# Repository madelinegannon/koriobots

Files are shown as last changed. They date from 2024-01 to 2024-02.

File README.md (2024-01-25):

# Koriobots
Koriobots are **cable-driven robots** that can be **dynamically choreographed** to make things float through mid-air. 
The koriobot platform is an open source toolkit aimed at unlocking **more imaginative experiences in robotics**: it is designed so that artists, architects, and designers can bring their creativity to **blend digital experiences with physical spaces**.

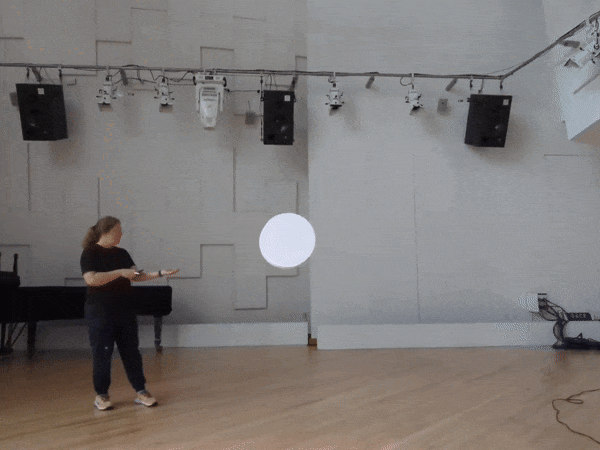
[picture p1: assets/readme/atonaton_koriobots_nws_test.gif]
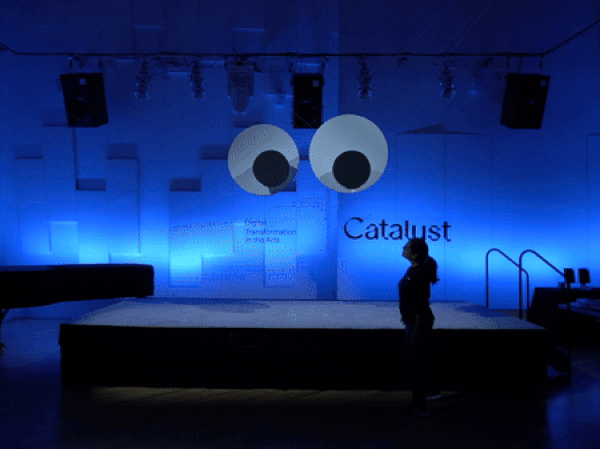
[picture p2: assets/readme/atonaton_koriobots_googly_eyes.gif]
|  |  |
| --- | --- |

## Overview
This reposity contains all the learning materials, fabrication files, BOMs, and software to create your own cable-driven robot systems. 

- See the [software](https://github.com/madelinegannon/koriobots/tree/main/software) directory for the koriobots server, third-party software templates, and example projects.
- See the [hardware](https://github.com/madelinegannon/koriobots/tree/main/hardware) to see the BOM and download 3D printable parts for making your own koriobots.
- See the [tutorials](https://github.com/madelinegannon/koriobots/tree/main/tutorials) directory to learn how to make and use koriobots.

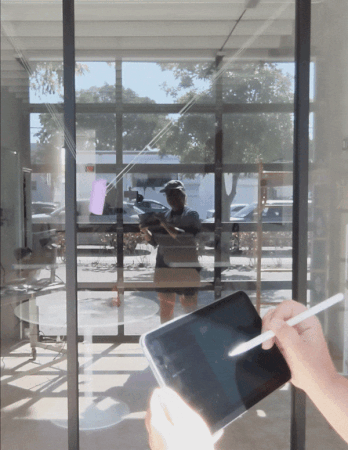
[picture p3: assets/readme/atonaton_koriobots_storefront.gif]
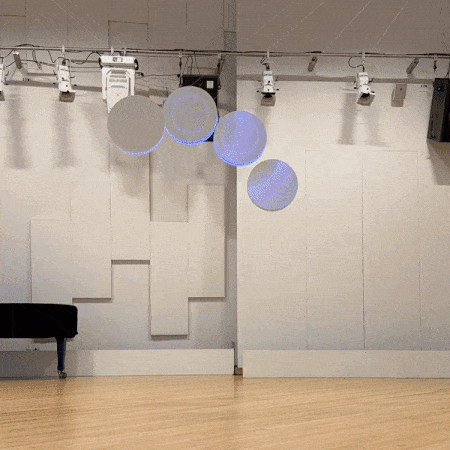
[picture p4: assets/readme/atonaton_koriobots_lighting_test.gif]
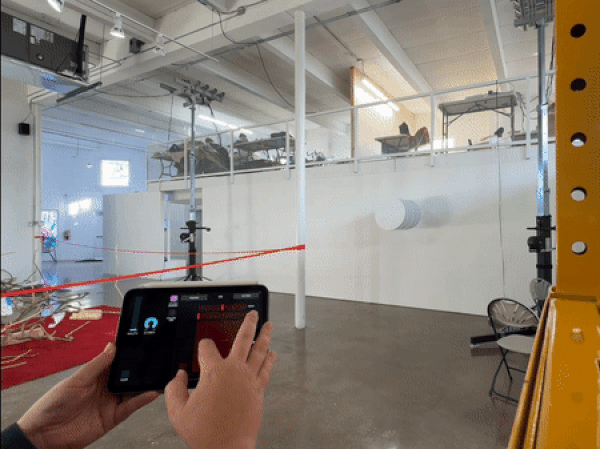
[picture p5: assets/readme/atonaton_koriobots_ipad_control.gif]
|  |  |  |
| --- | --- | --- |

## Motivations
Koriobots is intended as a functional, replicatable, and extensible reference design for professional-grade cable robots. The specified hardware strives to be more reliable _(and expensive)_ than DIY solutions, and more flexible, deployable _(and cheaper)_ than comparable industrial solutions. The control software is developed with interaction and performance at its core: it is extensible to external creative programming environments, and can be configured with automatic startup, homing, and shutdown for standalone art installations.

Cable-driven robots are the secret ingredient for many of the most magical and engaging kinetic installations of the past twenty years. Unfortunately, each artist group has had to build their own cable robots from scratch. By sharing this knowledge, we can spend less 
 time reinventing technical solutions, and more time on creative exploration. 

| _[Otto (2014~)](https://juerglehni.com/works/otto)_ by [Jürg Lehni](https://juerglehni.com/works) | _[Pendulums V (2015)](https://artcom.de/en/?project=pendulum-casa-v)_ by [ART+COM](https://artcom.de/en/department/art-en/) | _[In 20 Steps (2015)](https://studiodrift.com/work/in-20-steps/)_ by [Studio Drift](https://studiodrift.com/works/) | _[Kinds of Life (2019)](https://www.random-international.com/kinds-of-life)_ by [Random International](https://www.random-international.com/work) |
| --- | --- | --- | --- |
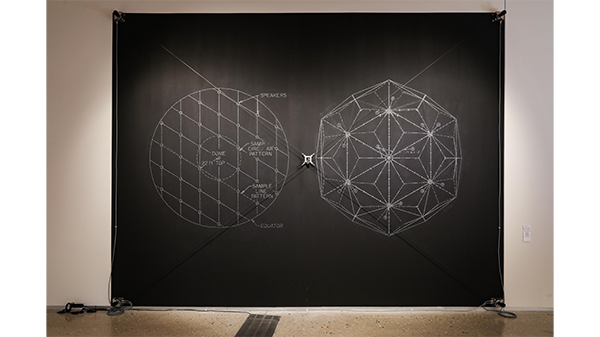
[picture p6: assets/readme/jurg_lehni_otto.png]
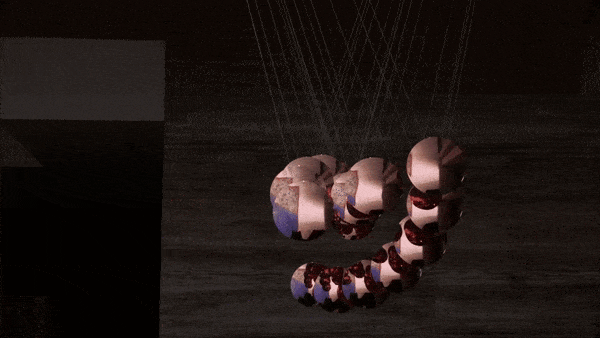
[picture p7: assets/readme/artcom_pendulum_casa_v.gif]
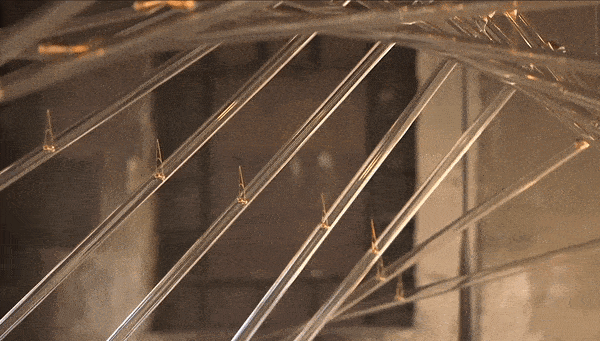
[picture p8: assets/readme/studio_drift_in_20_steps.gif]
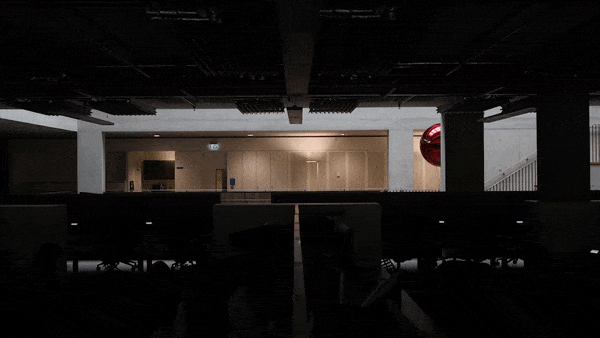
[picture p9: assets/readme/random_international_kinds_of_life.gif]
|  |  |  |  |

Our hope is that this knowledge repository can mitigate many of the technical hurdles of working with cable robots, and help to spark new forms of creative inquiry with this special type of robotic system.

## Contributing
The goal of this open source project is to grow and support many more usecases and audiences for cable-driven robots. We invite any and all contributions that extend the hardware, software, and learning materials for koriobots. Here are a few requests:
- Hardware
  - Additional mechanical design options for the cable drum.
  - Additional mounting options.
  - Additional end-effectors.
  - Alternative sources and specifications for the BOM.
- Software
  - Support for non-Teknic motors.
  - Improved velocity and position controllers.
  - Additional templates for third-party software integrations.
  - Additional examples showcasing different use cases and learning concepts.

## Acknowledgements
Koriobots was made possible through generous support from the [Knight Foundation](https://knightfoundation.org/challenges/knight-new-work/).
Special thanks to the [FIU RDF Lab](https://carta.fiu.edu/roboticslab/), [New World Symphony](https://www.nws.edu/), [Oolite Arts](https://oolitearts.org/), and [Locust Projects](https://www.locustprojects.org/) for housing our experiments throughout the development of this project. 

Koriobots was developed with [openFrameworks](https://openframeworks.cc/), an open source C++ toolkit for creative coding.

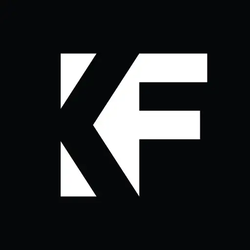
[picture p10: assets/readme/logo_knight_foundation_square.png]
Knight Foundation Logo
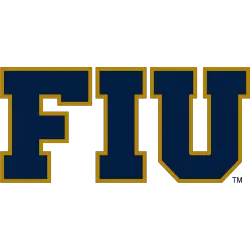
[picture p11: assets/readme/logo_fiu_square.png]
FIU Logo
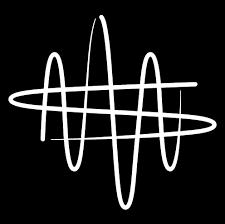
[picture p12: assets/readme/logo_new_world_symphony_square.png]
New World Symphony Logo
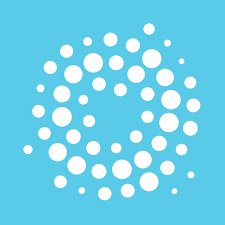
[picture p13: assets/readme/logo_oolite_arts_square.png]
Oolite Arts Logo
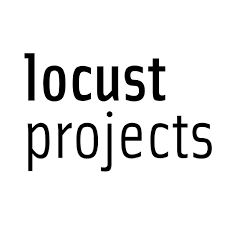
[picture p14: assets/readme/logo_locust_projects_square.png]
Locust Projects Logo
|  |  |  |  |  | 
| --- | --- | --- | --- | --- |

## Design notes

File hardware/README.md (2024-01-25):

# Koriobots Hardware

## Overview
The hardware of a Koriobots system is made up of the following components:

- Grooved Cable Drum
- Motor Controller
- Cable & Pulley
- Mounting Components
- End-Effector

Assemble the parts and prints following the [Assembly Tutorial](https://github.com/madelinegannon/koriobots/tree/main/hardware).

### Grooved Cable Drum
Each Koriobot uses a [grooved cable drum](https://wirerope.net/azwr/drums/#:~:text=%EF%80%82-,Drums%20%E2%80%93%20Grooved,-Drums%20are%20the) to reliably wind and unwind their cable. This cable-drum design was developed with mechanical simplicity and ease of production in mind. It features a [ClearPath-SC](https://www.teknic.com/files/downloads/Clearpath-SC%20User%20Manual.pdf) all-in-one servo motor system with full software control, a 3D printed grooved cable drum designed for 0.33mm diameter cable, and a shaft, couplings, standoffs and 3D printed mounts to connect everything together.

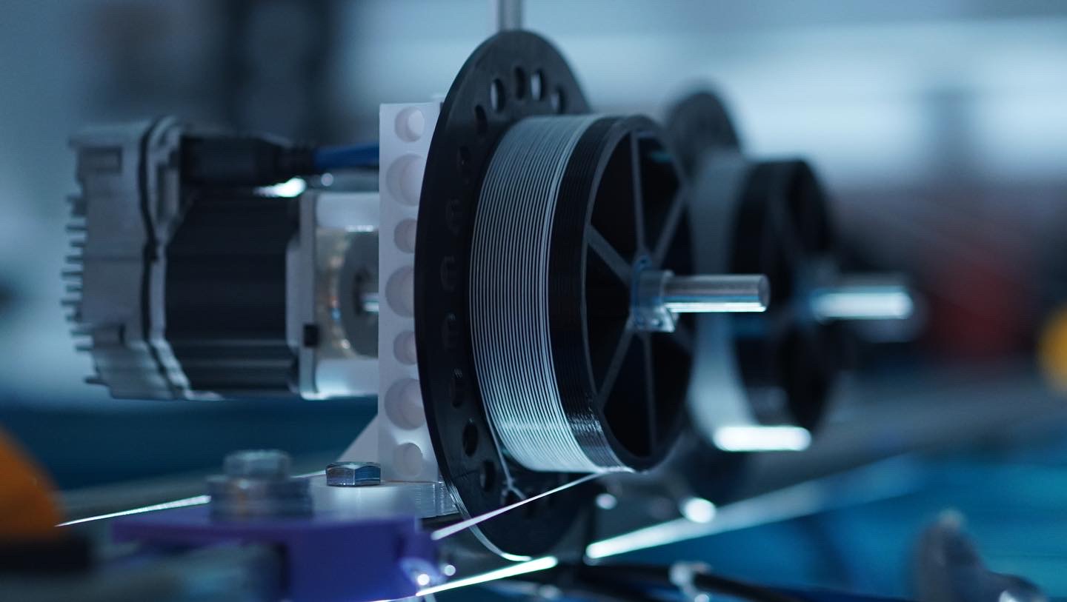
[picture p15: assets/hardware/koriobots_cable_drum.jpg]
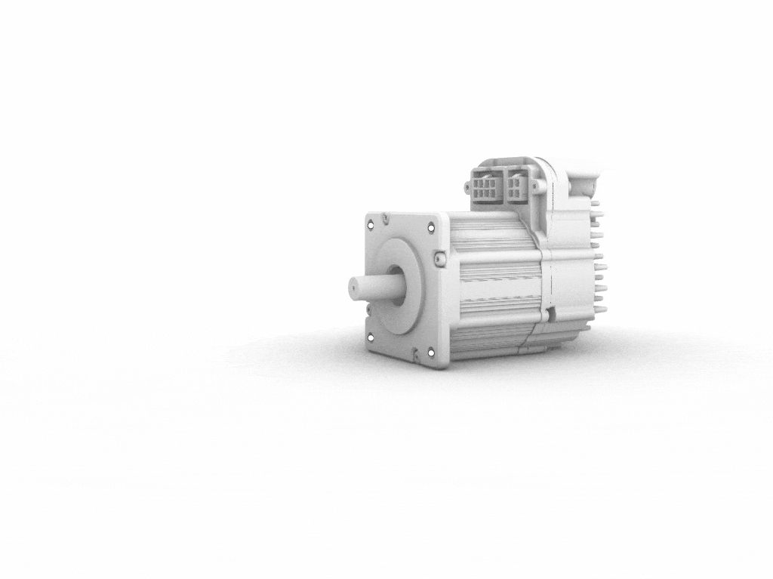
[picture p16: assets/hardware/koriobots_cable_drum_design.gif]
|  |  |
| --- | --- |

The provided 3D printed grooved cable drum holds over 6 meters (20 feet) of cable. You can modify the design of the drum to hold more or less cable based on your needs. 

### Motor Controller
Koriobots use the boards, cables, and power supplies specified by Teknic for their [ClearPath-SC](https://teknic.com/products/clearpath-brushless-dc-servo-motors/clearpath-sc/scsk-models/) motors. See the [BOM](https://github.com/madelinegannon/koriobots/tree/main/hardware/BOM.md) and Teknic's [ordering guide](https://teknic.com/clearpath-accessories-guide/accessories-guide-sc-dc/#overview) for complete list of required parts.

> The [`Manual_12oz_800_L.mtr`](https://github.com/madelinegannon/koriobots/blob/main/hardware/Manual_12oz_800_L.mtr) configuration file is here only as a reference. You should calibrate each of your motors based on your specific build, following Teknic's [instructions](https://www.teknic.com/files/downloads/Clearpath-SC%20User%20Manual.pdf) (page 52).

| [Communication Hub](https://teknic.com/SC4-HUB/) | [Power Hub](https://teknic.com/POWER4-HUB/) | [Motor Power Supply]() | [Logic Power Supply]() |
| --- | --- | --- | --- |
|  |  |  |  |
| Provides network connection for up to four ClearPath-SC motors. | Distributes DC bus power to up to four ClearPath motors. | Low Voltage (75 VDC) power supply for motor drive bus power. | General purpose logic power supply. |

### Cable & Pulley
Koriobots precisely position their end-effector by synchronously winding and un-winding their cables. We recommend using braided fishing line for light-weight applications. We have found that it is stiffer and stronger than conventional monofilament, and more available and pliable than thin-diameter wire cable. We have tested with [Sufix Advanced Superline 832 Braid 80lb](https://www.rapala.com/us_en/832-advanced-superline?childSku=us-660-080GH).

We integrate a small pulley for more precise positioning and routing of the cable. We've found it also helps prevent the cable drum from unspooling should the line lose tension. 
> Position the pulley at least 450mm (~18") from the cable drum for optimium spooling and unspooling.

### Mounting Components
We provide 3D printed files for mounting Koriobots to 3/8"-16 and M8 compatible fixtures, such as Unistrut, 45mm t-slot aluminum, and standard grip gear (like truss clamps).

|  |  |  |
| --- | --- | --- |

### End-Effectors
The end-effector is the thing that the koriobots are moving. You design this component based on your use case. Here are a few things to consider with your design:
- The Koriobots should connect at the Center of Mass of your end-effector.
- The end-effector will move more fluidly if its weight is symmetrically and bilaterally balanced.
- The end-effector should be heavy enough to keep the cable in tension throughout operation.
- The end-effector should not exceed the following recommend payloads that we have tested with this hardware design.

Maximum recommended payloads per configuration:
- 1D: 340g (0.75lb)
- 2D: 680g (1.50lb)
> _Note:_ The motors will overheat and shut off if overloaded, which will result in your payload falling.

[Plumb bobs](https://en.wikipedia.org/wiki/Plumb_bob) are a great default end-effector to start: they can be purchased in a number of weights and are symmetrical.

## Getting Started

1. Reference the [BOM](https://github.com/madelinegannon/koriobots/tree/main/hardware/BOM.md) to order the required parts.
2. Print the 3D models in the [`/cad_files`](https://github.com/madelinegannon/koriobots/tree/main/hardware/cad_files) folder.
3. Assemble the parts and prints following the [Assembly Tutorial]().

## Contributing
This design optimizes for mechanical simplicity, not efficiency. We welcome additional designs that maximize the torque, velocity, and mechanical efficiency of the cable drum design.

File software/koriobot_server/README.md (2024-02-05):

# Koriobot Server

The koriobot server is a software backend for controlling and coordinating teams of koriobots. You can run the server and communicate over OSC from many third-party applications, like Blender, TouchDesigner, Rhino/Grasshopper, and Unity. 

This README contains information about how to [Setup](https://github.com/madelinegannon/koriobots/tree/main/software/koriobot_server#setup) the sever, how to [Configure](https://github.com/madelinegannon/koriobots/tree/main/software/koriobot_server#configure) your koriobots through `configuration.xml` file, and how to send and receive data using the OSC-based [Sever API](https://github.com/madelinegannon/koriobots/tree/main/software/koriobot_server#server-api).

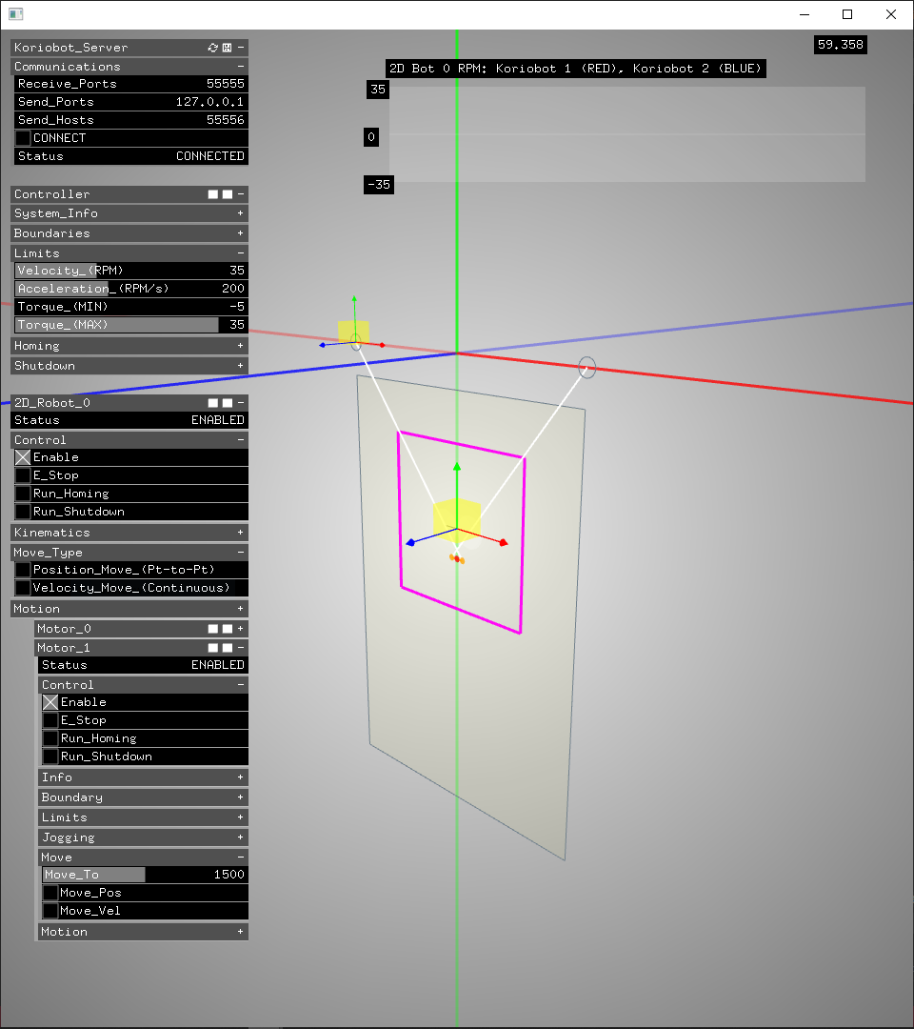
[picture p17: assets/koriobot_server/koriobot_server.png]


### Limitations
The koriobot server is only compatible with Windows 10/11. 

Tested On:
- Windows 10/11
- openFrameworks v0.11.2
- ClearView v1.7.15
- Visual Studio 2022

## Setup
There are two ways to get started using the Koriobot Server: download and install a standalone installer (quickest), or build the project from source code (most customizable).

### Installer

1. Download and install the Teknic ClearView SDK ([.zip file](https://teknic.com/files/downloads/ClearView_Install.zip)).
> _Note:_ If you  want to run ClearPath-SC motors without installing ClearView, just install the Clearpath Port Driver ([.zip file](https://teknic.com/files/downloads/ClearPath%20Port%20Driver%20Install.exe)).
2. Download and install the installer:  `koriobots_server_installer.exe` ([.exe file](https://github.com/madelinegannon/koriobots/blob/main/software/koriobot_server/koriobot_server_installer.exe)).
> _Note:_ If the software doesn't run, you may need to manually download and install the latest Microsoft Visual C++ Redistributable ([vc_redist.x64.exe file](https://aka.ms/vs/17/release/vc_redist.x64.exe)). More info from Microsoft [here](https://learn.microsoft.com/en-US/cpp/windows/latest-supported-vc-redist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).

### Build from Source

The koriobot server is built with [openFrameworks](https://openframeworks.cc/) — an open source C++ toolkit for creative coding — and the Teknic's ClearView SDK for controlling ClearPath-SC Series motors.

1. Download and install the Teknic ClearView SDK ([.zip file](https://teknic.com/files/downloads/ClearView_Install.zip))
2. Download and install [Microsoft Visual Studio 2022](https://visualstudio.microsoft.com/vs/community/)
     - Choose the Desktop Development with C/C++ workload
3. Download and install [openFrameworks v0.11.2](https://github.com/openframeworks/openFrameworks/releases/tag/0.11.2)
4. Install additional third-party addons: [ofxGizmo](https://github.com/NickHardeman/ofxGizmo)
5. Move the folder `/koriobot_server` into your `openFrameworks/apps/myApps` folder and build with the openFrameworks projectGenerator.
6. Build and Run the project in _Release x64_ mode in the IDE.

### Troubleshooting
- [How to install openFrameworks](https://openframeworks.cc/setup/vs/)
- [How to install an openFrameworks addon](https://openframeworks.cc/learning/01_basics/how_to_add_addon_to_project/)
- [How to use the openFrameworks projectGenerator](https://youtu.be/4k2ZcvC0YEA?si=gY0Y-3vlnC-ouL6y&t=252)

#### Teknic ClearPath Motors

- Teknic Downloads Website: https://teknic.com/downloads/
- Direct Download Teknic ClearView SDK [.zip file](https://teknic.com/files/downloads/ClearView_Install.zip)
- Examples are installed here: `C:\Program Files (x86)\Teknic\ClearView\sdk\examples`
- Source code & libraries are installed here: `C:\Program Files (x86)\Teknic\ClearView\sdk\sFoundation Source\sFoundation`

# Configuration File

Configure global settings for the koriobot system using an XML-based configuration file. These parameters are loaded everytime you run server.

- If you used the `Koriobot Server Installer`, your configuration file is located here: `C:\Program Files (x86)\ATONATON\Koriobot Server\data\configuration.xml`.
- If you built the project from source code, your configuration file is located here: `OF_PATH\apps\myApps\koriobot_server\bin\data\configuration.xml`.

The following code block documents what each configuration setting does:

```xml
<config>
    <!--1=1D, 2=2D, 3=3D-->
    <config_type>2</config_type>
    <!--Total number of koriobots-->
    <num_bots>2</num_bots>
    <!--OSC settings to send/receive messages-->
    <osc>
        <receive>
            <port>55555</port>
        </receive>
        <send>
            <host>127.0.0.1</host>
            <port>55556</port>
        </send>
    </osc>
    <!--System origin (in world coordinates)-->
    <origin>
        <X>-875.000000000</X>
        <Y>0.000000000</Y>
        <Z>0.000000000</Z>
        <QX>0.000000000</QX>
        <QY>0.000000000</QY>
        <QZ>0.000000000</QZ>
        <QW>1.000000000</QW>
    </origin>
    <!--Base reference position of each koriobot (in local coordinates)-->
    <bases>
        <pos>
            <X>0</X>
            <Y>0</Y>
            <Z>0</Z>
        </pos>
        <pos>
            <X>1750</X>
            <Y>0</Y>
            <Z>0</Z>
        </pos>
    </bases>
    <!--Motor Indices for 2D Configurations-->
    <motor_pairs>
        <pair>
            <A>0</A>
            <B>1</B>
        </pair>
    </motor_pairs>
    <!--Cable Drum Configuration-->
    <cable_drum>
        <!--1=LEFT-HANDED, 2=RIGHT-HANDED-->
        <direction>1</direction>
        <diameter_drum>99.000000000</diameter_drum>
        <diameter_cable>0.304800000</diameter_cable>
        <length>30</length>
        <turns>40</turns>
    </cable_drum>
    <!--End Effector Configuration-->
    <ee>
        <!--Offset from center of end-effector (in local coordinates)-->
        <offset>
            <X>100</X>
            <Y>0</Y>
            <Z>0</Z>
        </offset>
    </ee>
    <shutdown>
        <!--Position beyond bounds to lower koriobots before shutdown (in local coordinates)-->
        <pos>
            <X>0</X>
            <Y>3000</Y>
            <Z>0</Z>
        </pos>
    </shutdown>
    <!--Centroid, width, height of rectangular motion boundary (in World Coordinates)-->
    <bounds>
        <motion>
            <X>0</X>
            <Y>-1500.000000000</Y>
            <W>1750.0</W>
            <H>2600.0</H>
        </motion>
        <safety>
            <X>0</X>
            <Y>-1000.0</Y>
            <W>1000.0</W>
            <H>1000.0</H>
        </safety>
    </bounds>
    <!--Force Limits-->
    <limits>
        <velocity>35.0</velocity>
        <acceleration>200.0</acceleration>
        <torque>
            <MIN>-5</MIN>
            <MAX>35</MAX>
        </torque>
    </limits>
</config>
```

# Server API

| Message Address | Arg Format | Description |
| --- | --- | --- |
| /stop | —— | Trigger soft stop all koriobots |
| /move_vel | bool | Toggle velocity move on/off for all koriobots |
| /reset | —— | Trigger reset to the center of the safety bounds |
| /norm | int, float, float | Index and normalized {x,y} target coordinate. _Note: use index=-1 to move all koriobots to the normalized target._ |
| /limits/velocity | float | Sets the velocity limit for all koriobots |
| /limit/acceleration | float | Sets the acceleration limit for all koriobots |
| /bounds/pos | float, float | Sets normalized {x,y} position of the safety boundary |
| /bounds/width | float | Sets normalized width of the safety boundary |
| /bounds/height | float | Sets normalized height of the safety boundary |

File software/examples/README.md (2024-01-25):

# Examples
This folder has several useful starter projects in various programming environments. 
- Start the `Koriobot Server` before running these examples.
- See the descriptions below for usage details. 

## Processing
### koriobots_example_mouse2D.pde
Shows how to use your mouse to move the koriobots.
- Hover over the magenta rectangle to move the koriobot target.
- Press and drag the mouse to enable moving.
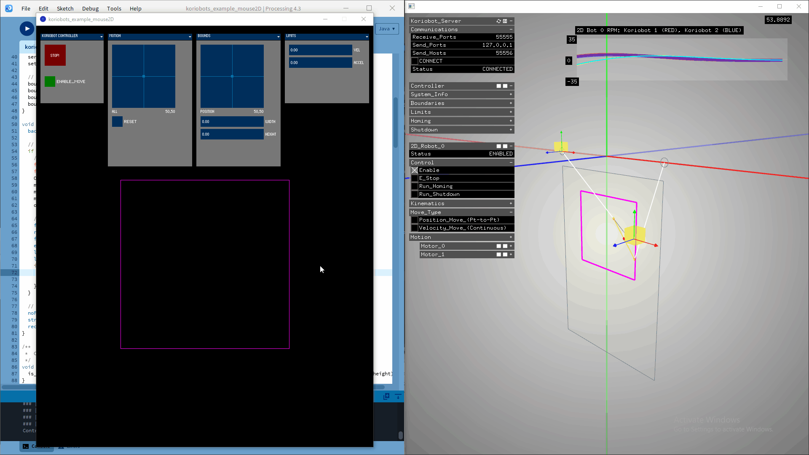
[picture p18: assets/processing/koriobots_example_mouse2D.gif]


### koriobots_example_physics2D.pde
Shows how to use physics simulation to move the koriobots.
- Install the [Box2D-for-Processing](https://github.com/shiffman/Box2D-for-Processing/tree/master/Box2D-for-Processing/dist) library.
- Press and drag the mouse to throw the box around.
- Toggle the `Enable Move` button to enable moving.
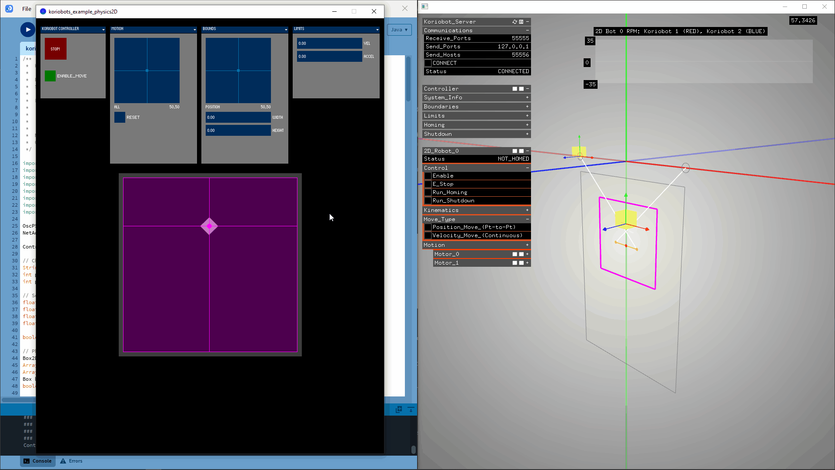
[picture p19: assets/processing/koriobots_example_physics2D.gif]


## Grasshopper
#### koriobots_example_follow_path.gh
Shows how to move the koriobots to follow a path. Useful for pick-and-place operations
- Open _koriobots_example_follow_path.3dm_, start Grasshopper, then open _koriobots_example_follow_path.gh_ inside Grasshopper.
- Update the `Evaulate Curve` slider to move the koriobot target.
- Toggle the `\move_vel` button `ON` to enable moving.
  
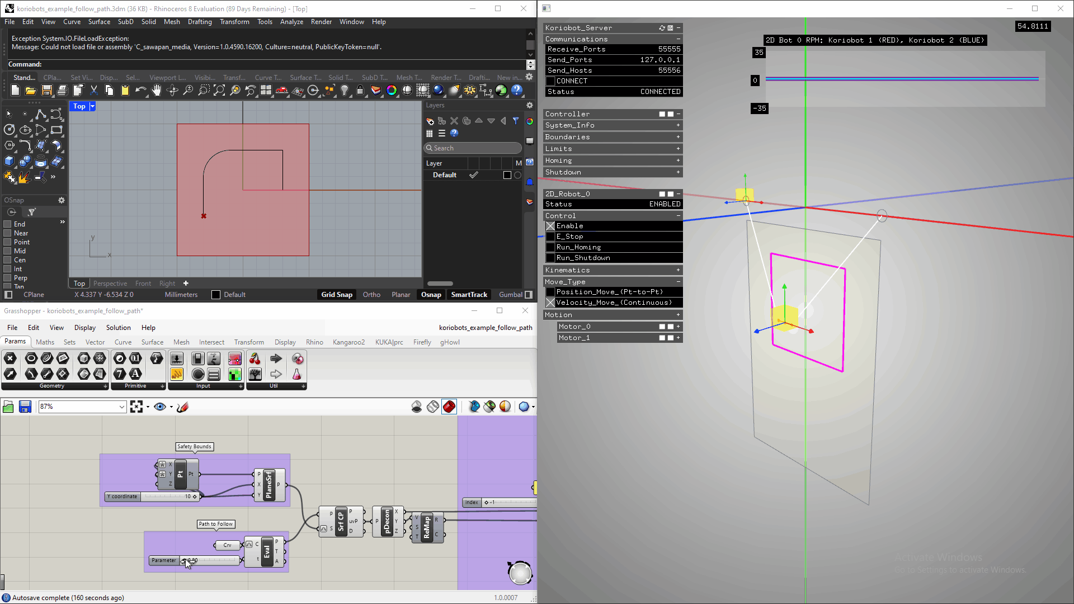
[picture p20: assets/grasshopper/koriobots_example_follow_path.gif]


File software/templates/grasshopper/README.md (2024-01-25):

# Grasshopper Template

[Grasshopper](https://www.rhino3d.com/#:~:text=Kay%2C%20Kiteboard%20Shaper-,Grasshopper,-Grasshopper%20is%20a) is a visual programming environment inside of the popular CAD software, [Rhinoceros 3D](https://www.rhino3d.com/). 

We can use Grasshopper and the [python-osc](https://pypi.org/project/python-osc/) python library to talk to the Koriobot Sever:

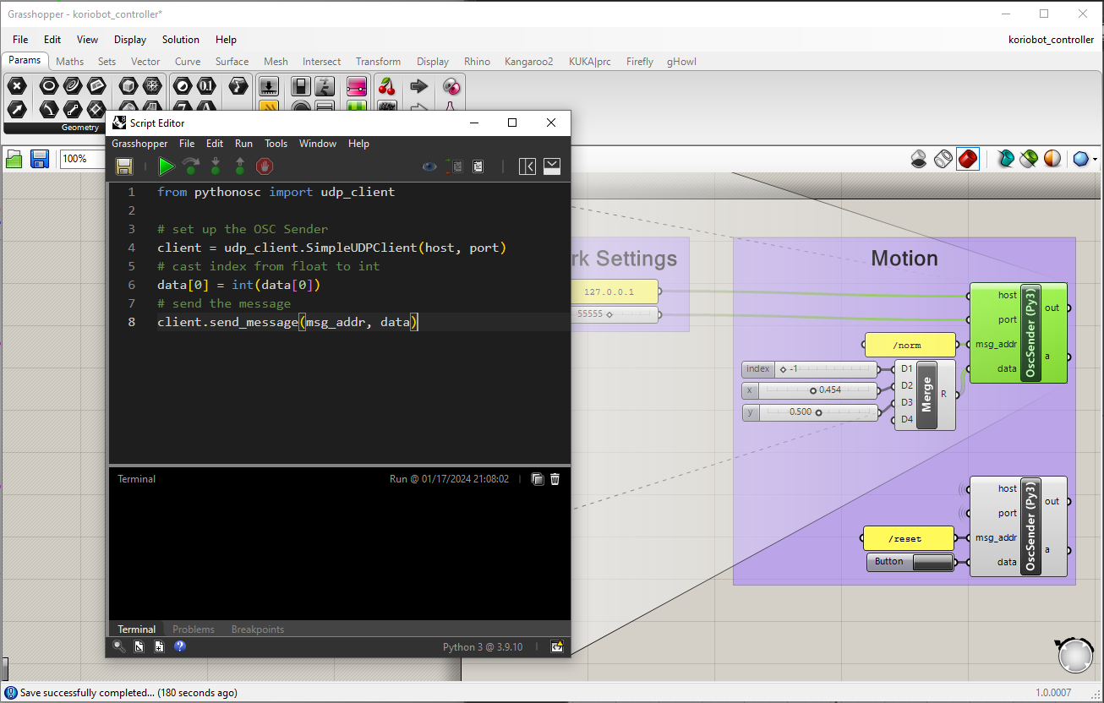
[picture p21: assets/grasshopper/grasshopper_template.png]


## Setup

1. Download and install Rhino 8
> There's a free 90 day trial.
2. Open Grasshopper and add a Python 3 Script to the canvas. 
3. Double Click to open the Python Script Editor.
4. Run the following script to locate where Rhino's contained version of python is stored on your computer:

```
import sys
println(sys.path)
```
> The path should be something like `~\.rhinocode\py39-rh8\`

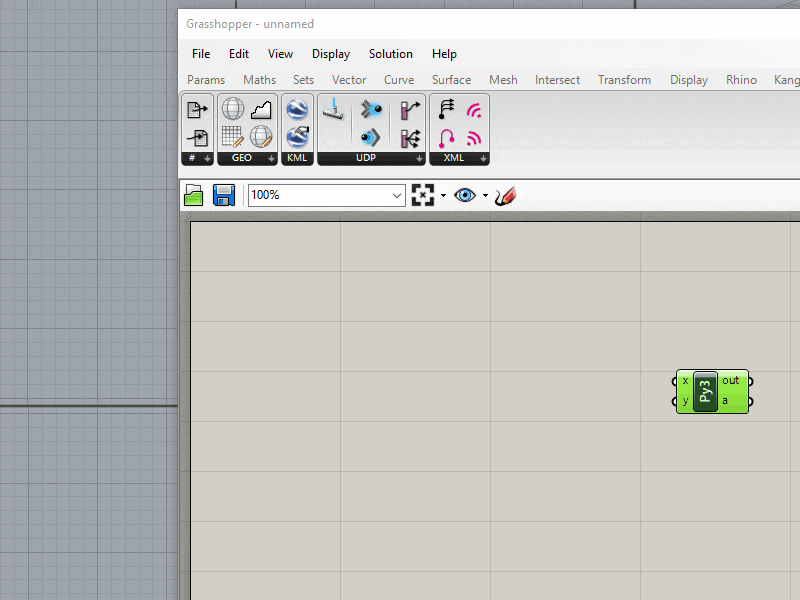
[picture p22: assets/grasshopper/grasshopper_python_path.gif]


5. The `~\.rhinocode\py39-rh8\lib` folder is where we need to add external python libraries for Rhino.
6. Install `python-osc` via pip. Open a terminal, and run the command:

```shell
cd ~\.rhinocode\py39-rh8
pip install --target=.\lib python-osc
```
> You will be prompted to install `pip` if you haven't yet.

### Optional Step:
<details>
<summary>How to manually copy/paste system-wide python library into Rhino's version of python:</summary>
<br>
If the local <b>pip install</b> doesn't work, you can install the library system-wide and copy/paste into Rhino's internal version of python.
<brGo to where `python-osc` was installed, copy the folder, and paste it back into Rhino's internal python library folder.
<br><br> The system-wide library path should be something like <i>~\AppData\Local\Programs\Python\Python310\Lib\site-packages</i>
<br><br>
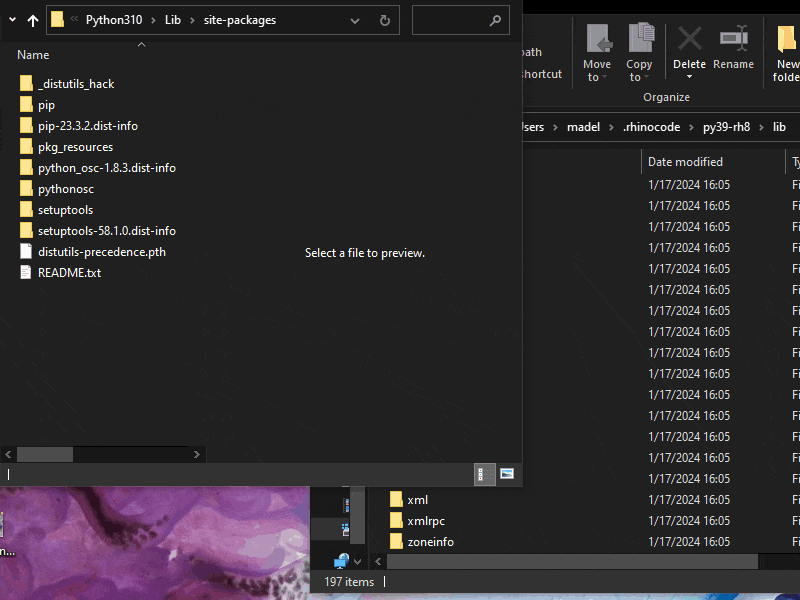
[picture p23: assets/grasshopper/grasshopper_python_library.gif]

</details>

7. Restart Rhino, load Grasshopper, and open `koriobot_controller.gh`. Interact with the sliders or buttons to send a value to the Koriobot Server.

## Notes

- Tested on Windows 10/11, Rhino 8, python 3.9, and python-osc 1.8.3

## Code Reference
These python snippets are the code running inside each of the grasshopper template's _OscSender_ nodes.

```python
# Controls: /stop and /move_vel code
from pythonosc import udp_client

# set up the OSC Sender
client = udp_client.SimpleUDPClient(host, port) 
# send the message       
client.send_message(msg_addr, data)
```

```python
# Motion: /norm code
from pythonosc import udp_client

# set up the OSC Sender
client = udp_client.SimpleUDPClient(host, port)
# cast index from float to int
data[0] = int(data[0])   
# send the message       
client.send_message(msg_addr, data)
```

```python
# Motion: /reset code
from pythonosc import udp_client

# set up the OSC Sender
client = udp_client.SimpleUDPClient(host, port)
# cast index from float to int
data[0] = int(data[0])   
# send the message       
client.send_message(msg_addr, data)
```

```python
# Bounds: /bounds code
from pythonosc import udp_client

# set up the OSC Sender
client = udp_client.SimpleUDPClient(host, port)
 
# send the message
addr = msg_addr + "/pos"  
val = [data[0], data[1]]
client.send_message(addr, val)

addr = msg_addr + "/width"  
val = data[2]
client.send_message(addr, val)

addr = msg_addr + "/height"  
val = data[3]
client.send_message(addr, val)
```

```python
# Motion: /limits code
from pythonosc import udp_client

# set up the OSC Sender
client = udp_client.SimpleUDPClient(host, port)
 
# send the message
addr = msg_addr + "/velocity"  
val = data[0]
client.send_message(addr, val)

addr = msg_addr + "/acceleration"  
val = data[1]
client.send_message(addr, val)
```

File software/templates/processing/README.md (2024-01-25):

# Processing Template

[Processing](https://processing.org/) is a creative coding platform for sketching with code. 

We can use Processing and the third-party library [oscP5](https://sojamo.de/libraries/oscP5/) to talk to the Koriobot Sever:

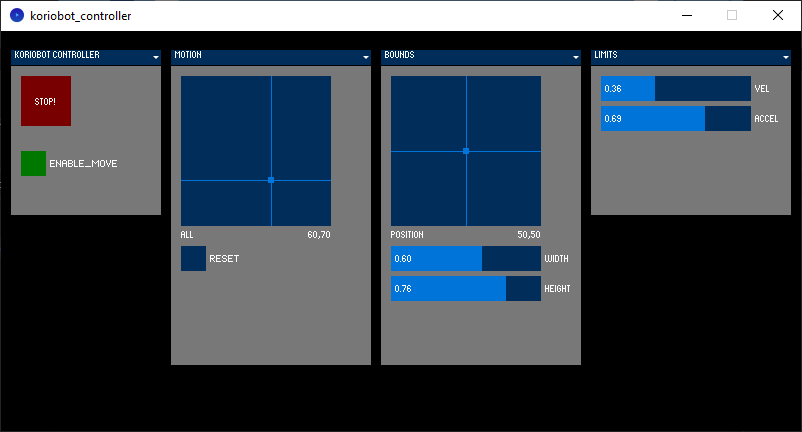
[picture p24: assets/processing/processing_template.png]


## Setup

1. Download and install [Processing](https://processing.org/download).
2. Download and install [oscP5](https://sojamo.de/libraries/oscP5/) following these [instructions](https://sojamo.de/libraries/oscP5/#installation).
3. Copy `koriobot_controller.pde` into your Processing Sketchbook.
4. Configure your network settings:



6. Press play and run.

## Notes

- Tested on Processing 4.3, oscP5 0.9.8, and controlP5 2.2.5

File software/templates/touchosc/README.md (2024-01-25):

# TouchOSC Template

[TouchOSC](https://hexler.net/touchosc) is an easy-to-use interface builder that can send and receive [OSC](https://ccrma.stanford.edu/groups/osc/index.html) messages from multiple sources. It's the quickest way to build your own interactive touch interface on your desktop, phone, or tablet — _plus_ it's supported on nearly every operating system: Windows / macOS / Linux / iOS / Android / RasPi.

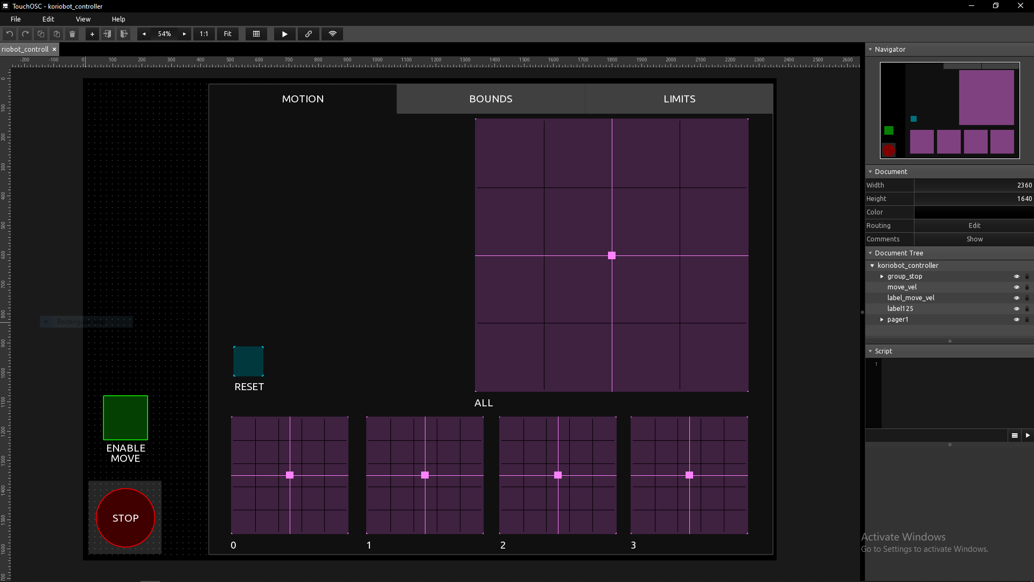
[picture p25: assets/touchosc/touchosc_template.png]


We can use TouchOSC to talk to the Koriobot Sever:



## Setup

1. Download TouchOSC for your platform [here](https://hexler.net/touchosc#get).
> The desktop version is free.
2. Open TouchOSC and configure your network settings.

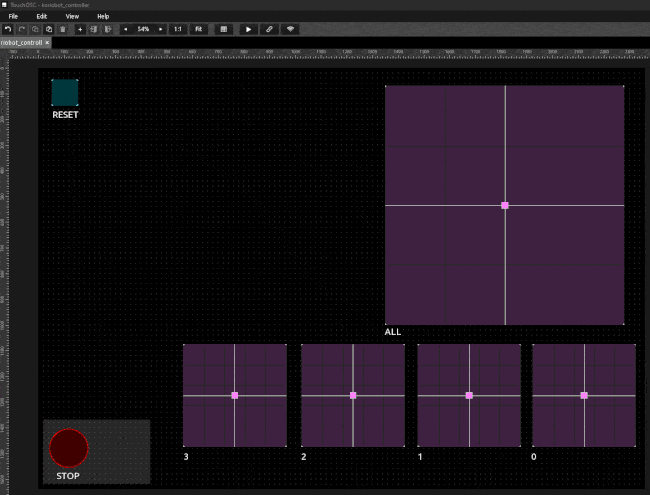
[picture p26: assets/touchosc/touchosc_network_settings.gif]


3. Open a template file in TouchOSC and press the play button to start running the file.
4. Press the dot in the upper right corner to close the file.

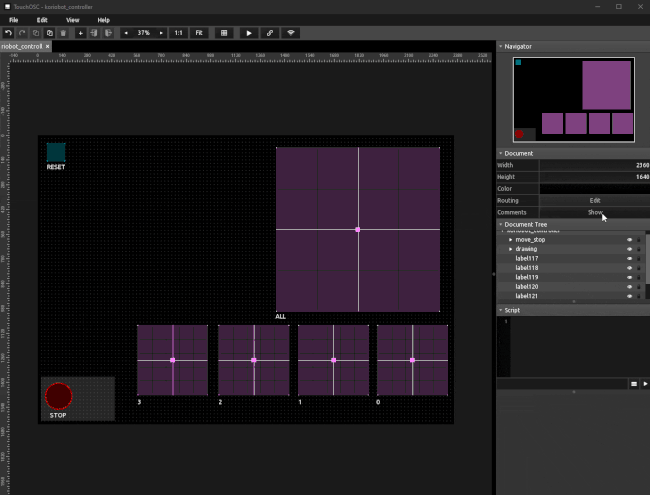
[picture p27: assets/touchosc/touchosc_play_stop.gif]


## Notes

- Tested on TouchOSC 1.2.7.190

## Troubleshooting

- [TouchOSC User Manual](https://hexler.net/touchosc/manual/introduction)

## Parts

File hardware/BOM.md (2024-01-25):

# Bill of Materials

The following table lists the parts and costs for building your own koriobot system. Prices are based in USD for purchases made in 2023. 
One motor is specified in the BOM, however the total cost is not a per-motor cost: there are several items that can be used for multiple koriobots.

We recommend following Teknic's [ordering guide](https://teknic.com/clearpath-accessories-guide/accessories-guide-sc-dc/#overview) to determine the final number of motors, boards, cables, and power supplies needed for your specific system.

🔗 See the google sheet of the following table [here](https://docs.google.com/spreadsheets/d/1K7qIrnV9r5dMJWnOKxVrk1uVV2S3eMcffBsYf00h5N8/edit?usp=sharing).

| Part Name | Sub-Assembly | Part Number | Supplier | Reference | Quantity | Unit Price | Cost | Notes |
| --- | --- | --- | --- | --- | --- | --- | --- | --- |
| ClearPath Integrated Servo Motor | Cable Drum | CPM-SCSK-2310S-RLNA | [Teknic](https://teknic.com/) | [https://teknic.com/model-info/CPM-SCSK-2310S-RLNA](https://teknic.com/model-info/CPM-SCSK-2310S-RLNA) | 1 | $333.00 | $333.00 | Purchase 1 for every ClearPath Motor. |
| Controller Cable, 10 ft | Cable Drum | CPM-CABLE-CTRL-MU120 | [Teknic](https://teknic.com/) | [https://teknic.com/CPM-CABLE-CTRL-MU120/](https://teknic.com/CPM-CABLE-CTRL-MU120/) | 1 | $23.00 | $23.00  | Purchase 1 for every ClearPath Motor. |
| DC Power Cable, IPC (or hub) to ClearPath, 10 ft | Cable Drum | CPM-CABLE-PWR-MS120 | [Teknic](https://teknic.com/) | [https://teknic.com/CPM-CABLE-PWR-MS120/](https://teknic.com/CPM-CABLE-PWR-MS120/) | 1 | $19.00 | $19.00  | Purchase 1 for every ClearPath Motor. |
| 350/500 Watt DC Power Supply | Motor Controller | IPC-5 | [Teknic](https://teknic.com/) | [https://teknic.com/IPC-5](https://teknic.com/IPC-5) | 1 | $248.00 | $248.00 | Purchase 1 for every 8 ClearPath Motors. |
| AC Power Cable for IPC-3 and IPC-5 | Motor Controller | IPC35-CABLE110 | [Teknic](https://teknic.com/) | [https://teknic.com/IPC35-CABLE110/](https://teknic.com/IPC35-CABLE110/) | 1 | $14.00 | $14.00  | |
| Communication Hub for ClearPath-SC Series | Motor Controller | SC4-HUB | [Teknic](https://teknic.com/) | [https://teknic.com/SC4-HUB](https://teknic.com/SC4-HUB) | 1 | $49.00 | $49.00  | Purchase 1 for every 4 ClearPath Motors. |
| 24 VDC Power Supply | Motor Controller | PWR-IO-24VDC | [Teknic](https://teknic.com/) | [https://teknic.com/PWR-IO-24VDC/](https://teknic.com/PWR-IO-24VDC/) | 1 | $39.00 | $39.00  | |
| 24 Volt Power, 2-Pin Molex Cable | Motor Controller | CPM-CABLE-M2P2P-120 | [Teknic](https://teknic.com/) | [https://teknic.com/CPM-CABLE-M2P2P-120/](https://teknic.com/CPM-CABLE-M2P2P-120/) | 2 | $13.00 | $26.00  | |
| DC Power Distribution Hub | Motor Controller | POWER4-HUB | [Teknic](https://teknic.com/) | [https://teknic.com/POWER4-HUB/](https://teknic.com/POWER4-HUB/) | 1 | $49.00 | $49.00  | Purchase 1 for every 4 ClearPath Motors. |
| DC Power Cable, IPC to POWER4-HUB, 6 ft | Motor Controller | PC-SBR-72 | [Teknic](https://teknic.com/) | [https://teknic.com/PC-SBR-72/](https://teknic.com/PC-SBR-72/) | 1 | $18.00 | $18.00  | |
| 3408 Series V-Groove Pulley - 2 Pack | Cable Pulley | 3408-0001-0001 | [ServoCity](https://www.servocity.com/) | [https://www.servocity.com/3408-series-v-groove-pulley-2-pack/](https://www.servocity.com/3408-series-v-groove-pulley-2-pack/) | 1 | $7.50 | $7.50 | |
| 0.375" to 0.375" Clamping Shaft Coupler | Cable Drum | 625064 | [ServoCity](https://www.servocity.com/) | [https://www.servocity.com/0-375-to-0-375-clamping-shaft-coupler-1/](https://www.servocity.com/0-375-to-0-375-clamping-shaft-coupler-1/) | 2 | $5.00 | $10.00  | |
| 0.375" (3/8") x 4.00" Stainless Steel Precision Shafting | Cable Drum | 634208 | [ServoCity](https://www.servocity.com/) | [https://www.servocity.com/0-375-3-8-x-4-00-stainless-steel-precision-shafting/](https://www.servocity.com/0-375-3-8-x-4-00-stainless-steel-precision-shafting/) | 1 | $2.60 | $2.60 | |
| Flanged Ball Bearing (7/8" OD, 9/32" Thickness) - 2 Pack | Cable Drum | 1601-0001-0375 | [ServoCity](https://www.servocity.com/) | [https://www.servocity.com/3-8-id-x-7-8-od-flanged-ball-bearing-2-pack/](https://www.servocity.com/3-8-id-x-7-8-od-flanged-ball-bearing-2-pack/) | 1 | $4.00 | $4.00 | |
| Thrust Ball Bearing (12mm ID x 21mm OD, 5mm Thickness) | Cable Drum | 1613-0521-0012 | [ServoCity](https://www.servocity.com/) | [https://www.servocity.com/12mm-id-thrust-ball-bearing-12mm-id-x-21mm-od-5mm-thickness/](https://www.servocity.com/12mm-id-thrust-ball-bearing-12mm-id-x-21mm-od-5mm-thickness/) | 1 | $5.00 | $5.00 | |
| Aluminum Spacers (10 Pack) M5 ID, M10 OD, 35mm | Cable Drum | 1040-Pack | [OpenBuilds](https://openbuildspartstore.com/) | [https://openbuildspartstore.com/aluminum-spacers-10-pack/](https://openbuildspartstore.com/aluminum-spacers-10-pack/) | 1 | $6.00 | $6.00 | |
| Socket Head Screw M5-0.8 x 45 mm, 50 PK | Cable Drum | 22UC42 | [Grainger](https://www.grainger.com/) | [https://www.grainger.com/product/APPROVED-VENDOR-Socket-Head-Cap-Screw-M5-0-22UC42](https://www.grainger.com/product/APPROVED-VENDOR-Socket-Head-Cap-Screw-M5-0-22UC42) | 1 | $15.66 | $15.66  | |
| Sufix Advanced Superline 832 Braid 80 lb Ghost | Cable | ‎660-080GH | [Rapala](https://www.rapala.com/) | [https://www.rapala.com/us_en/832-advanced-superline?childSku=us-660-080GH](https://www.rapala.com/us_en/832-advanced-superline?childSku=us-660-080GH) | 1 | $20.00 | $20.00  | Available on [Amazon](https://www.amazon.com/gp/product/B0080SNENY). |
| Threaded Insert Assortment | Cable Drum | GE-KASTEN-001 | [ruthex](https://www.ruthex.de/en/collections/gewindeeinsatze) | [https://www.amazon.com/gp/product/B08K1BVGN9](https://www.amazon.com/gp/product/B08K1BVGN9) | 1 | $34.00 | $34.00  | Available on [Amazon](https://www.amazon.com/gp/product/B08K1BVGN9). |
| Unistrut 10', 12-gauge | Mounting | 202714274 | [Home Depot](https://www.homedepot.com/) | [https://www.homedepot.com/p/Superstrut-10-ft-12-Gauge-Half-Slotted-Metal-Framing-Strut-Channel-in-Silver-Galvanized-ZA12HS10EG/202714274](https://www.homedepot.com/p/Superstrut-10-ft-12-Gauge-Half-Slotted-Metal-Framing-Strut-Channel-in-Silver-Galvanized-ZA12HS10EG/202714274) | 1 | $35.00 | $35.00  | Available at many local hardware stores. |
| 3/8 in.-16 x 1 in. Zinc Plated Hex Bolt (25-Pack) | Mounting | 204281551 | [Home Depot](https://www.homedepot.com/) | [https://www.homedepot.com/p/Everbilt-3-8-in-16-x-1-in-Zinc-Plated-Hex-Bolt-25-Pack-800820/204281551](https://www.homedepot.com/p/Everbilt-3-8-in-16-x-1-in-Zinc-Plated-Hex-Bolt-25-Pack-800820/204281551) | 1 | $6.40 | $6.40 | Available at many local hardware stores. |
| 3/8 in. Strut Channel Spring Nut (5-Pack) | Mounting | 100179881 | [Home Depot](https://www.homedepot.com/) | [https://www.homedepot.com/p/Superstrut-3-8-in-Strut-Channel-Spring-Nut-5-Pack-ZA1003-8EG-10/100179881](https://www.homedepot.com/p/Superstrut-3-8-in-Strut-Channel-Spring-Nut-5-Pack-ZA1003-8EG-10/100179881) | 1 | $7.90 | $7.90 | Available at many local hardware stores. |
| Koriobot Grooved Cable Drum for .33mm cable | Cable Drum | koriobot_grooved_cable_drum_0.33 | [Koriobots](https://github.com/madelinegannon/koriobots) | [STL](https://github.com/madelinegannon/koriobots/blob/main/hardware/cad_files/koriobot_grooved_cable_drum_0_33.stl), 3DM | 1 | | | |
| Koriobot Pulley Block for 3408 V-Groove Pulley | Cable Pulley | koriobot_pulley_block_3408 | [Koriobots](https://github.com/madelinegannon/koriobots) | [STL](https://github.com/madelinegannon/koriobots/blob/main/hardware/cad_files/koriobot_pulley_block_3408.stl), 3DM | 1 | | | |
| Koriobot Motor Mount | Cable Drum | koriobot_nema_23_mount | [Koriobots](https://github.com/madelinegannon/koriobots) | [STL](https://github.com/madelinegannon/koriobots/blob/main/hardware/cad_files/koriobot_nema_23_mount.stl), 3DM | 1 | | | |
| Koriobot Motor to Unistrut Adapter | Mounting | koriobot_nema_23_to_unitstrut | [Koriobots](https://github.com/madelinegannon/koriobots) | [STL](https://github.com/madelinegannon/koriobots/blob/main/hardware/cad_files/koriobot_nema_23_to_unitstrut.stl), 3DM | 1 | | | |
| | | | | | | TOTAL | $972.06 | \*Not representative of a per-motor cost |

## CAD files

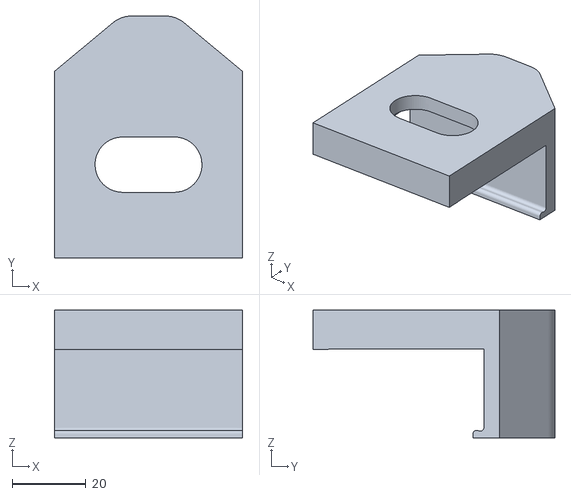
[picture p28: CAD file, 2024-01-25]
hardware/cad_files/koriobot_pulley_block_3408.stl
51.0 x 65.6 x 34.7

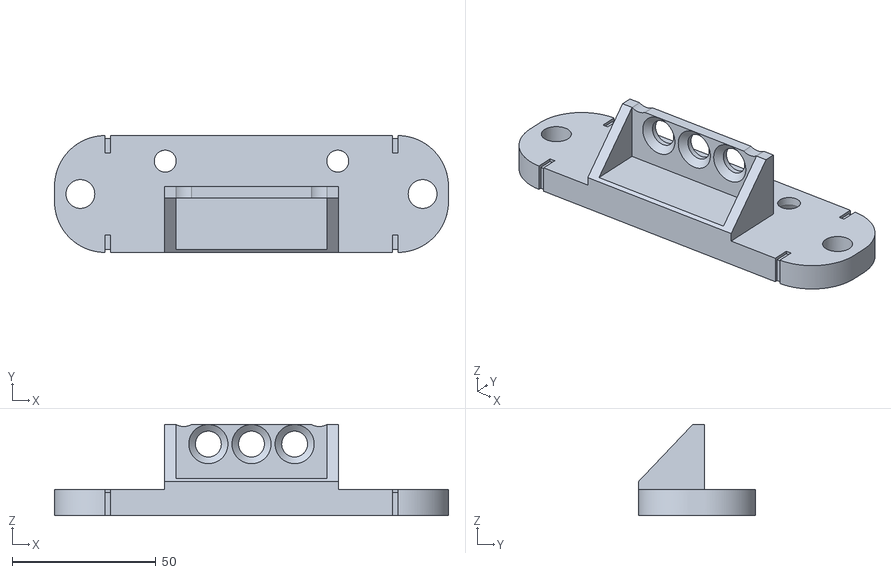
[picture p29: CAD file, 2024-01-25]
hardware/cad_files/koriobot_nema_23_to_unitstrut.stl
137.0 x 40.6 x 31.7

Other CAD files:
software/examples/grasshopper/koriobots_example_follow_path.3dm

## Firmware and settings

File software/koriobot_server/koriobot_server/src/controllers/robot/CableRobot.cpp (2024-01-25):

#include "CableRobot.h"


CableRobot::CableRobot(ClearPathMotor* motor, ofxXmlSettings config)
{
	this->motor = motor;

	configure(config);
	setup_gui();
	motor->set_motion_params(limit_velocity.get(), limit_acceleration.get());

	check_for_system_ready();

	setup_plots();
}

void CableRobot::configure(ofxXmlSettings config)
{
	this->config = config;
	// Save the origin (Global Coordinate
	float x = config.getValue("config:origin:X", 0);
	float y = config.getValue("config:origin:Y", 0);
	float z = config.getValue("config:origin:Z", 0);
	float qx = config.getValue("config:origin:QX", 0);
	float qy = config.getValue("config:origin:QY", 0);
	float qz = config.getValue("config:origin:QZ", 0);
	float qw = config.getValue("config:origin:QW", 0);
	this->origin = new ofNode();
	this->origin->setGlobalPosition(glm::vec3(x, y, z));
	this->origin->setGlobalOrientation(glm::quat(qw, qx, qy, qz));
	this->origin->rotateAroundDeg(180, glm::vec3(1, 0, 0), glm::vec3(0, 0, 0));

	// Set the base (Local Coordinates)
	config.pushTag("config");
	config.pushTag("bases");
	config.pushTag("pos", motor->get_motor_id());
	glm::vec3 p = glm::vec3();
	p.x = config.getValue("X", 0);
	p.y = config.getValue("Y", 0);
	p.z = config.getValue("Z", 0);
	base.setParent(*origin);
	base.setPosition(p);
	config.popTag();
	config.popTag();
	config.popTag();

	// Setup the Cable Drum
	int cable_drum_dir = config.getValue("config:cable_drum:direction", 0);
	drum.direction = cable_drum_dir < 2 ? Groove::LEFT_HANDED : Groove::RIGHT_HANDED;
	drum.diameter_drum = config.getValue("config:cable_drum:diameter_drum", 0);
	drum.diameter_cable = config.getValue("config:cable_drum:diameter_cable", 0.0);
	drum.length = config.getValue("config:cable_drum:length", 0);
	drum.turns = config.getValue("config:cable_drum:turns", 0);
	drum.initialize(drum.direction, drum.diameter_drum, drum.length, drum.turns);

	// Define the linear length per motor step
	float step_resolution = motor->get_resolution();
	mm_per_count = drum.circumference / step_resolution;

	// Setup the kinematic chain
	tangent.setParent(this->base);
	//tangent.setPosition(drum.get_tangent());
	target.setPosition(0, 0, 0);
	actual.setParent(tangent);
	actual.setPosition(0, 0, 0);

	ee_offset = config.getValue("config:ee:offset:X", 0);

	x = config.getValue("config:bounds:motion:X", 0);
	y = config.getValue("config:bounds:motion:Y", 0);
	float width = config.getValue("config:bounds:motion:W", 0);
	float height = config.getValue("config:bounds:motion:H", 0);
	bounds_motion.setFromCenter(x, y, width, height);
	this->bounds_min = (y + height / 2) * -1;
	this->bounds_max = (y - height / 2) * -1;

	// Set the force limits
	limit_velocity = config.getValue("config:limits:velocity", 0);
	limit_acceleration = config.getValue("config:limits:acceleration", 0);
	limit_torque_min = config.getValue("config:limits:torque:MIN", 0);
	limit_torque_max = config.getValue("config:limits:torque:MAX", 0);

	// if the external ee node is empty, create a new one that is internal and add a gizmo
	if (ee->getGlobalPosition() == glm::vec3() && ee->getGlobalOrientation() == glm::quat()) {
		ee = new ofNode();
		ee->setParent(tangent);
		ee->setPosition(0, -1 * (bounds_max.get() - bounds_min.get()) / 2, tangent.getGlobalPosition().z);
		target.setParent(*ee);

		gizmo_ee.setNode(*ee);
		gizmo_ee.setDisplayScale(.5);
		gizmo_ee.setTranslationAxisMask(IGizmo::AXIS_Y);
		gizmo_ee.setRotationAxisMask(IGizmo::AXIS_Z);
	}
	// otherwise, parent the target to the external ee and offset by ee_offset value
	else {
		target.setParent(*ee);
		target.setGlobalPosition(ee->getGlobalPosition());
		if (motor->get_motor_id() % 2 == 0)
			target.setPosition(-1 * ee_offset, 0, 0);
		else
			target.setPosition(ee_offset, 0, 0);

		gizmo_ee.setNode(*ee);
		gizmo_ee.setDisplayScale(.5);
		gizmo_ee.setRotationAxisMask(IGizmo::AXIS_Z);
	}
}

float CableRobot::get_position_actual()
{
	return count_to_mm(motor->get_position(false), true);
}

/**
 * @brief Returns the main motion parameters for the robot.
 *
 * @return (vector<float>)  params: { limit_velocity, limit_acceleration, bounds_min, bounds_max }
 */
vector<float> CableRobot::get_motion_parameters()
{
	vector<float> params;
	params.push_back(limit_velocity.get());
	params.push_back(limit_acceleration.get());
	params.push_back(bounds_min.get());
	params.push_back(bounds_max.get());
	return params;
}

/**
 * @brief Sets the main motion parameters for the robot.
 *
 * @param (float)  velocity_max: velocity limit (RPM)
 * @param (float)  accel_max: acceleration limit (RPM/s)
 * @param (float)  position_min: minimum position bounds
 * @param (float)  position_max: maximum position bounds
 */
void CableRobot::set_motion_parameters(float velocity_max, float accel_max, float position_min, float position_max)
{
	limit_velocity.set(velocity_max);
	limit_acceleration.set(accel_max);
	bounds_min.set(position_min);
	bounds_max.set(position_max);
}

/**
 * @brief Returns the main motion parameters for the robot.
 *
 * @return (vector<float>)  params: { jogging_vel_limit, jogging_accel_limit, jogging_distance }
 */
vector<float> CableRobot::get_jogging_parameters()
{
	vector<float> params;
	params.push_back(jog_vel.get());
	params.push_back(jog_accel.get());
	params.push_back(jog_dist.get());
	return params;
}

void CableRobot::set_jogging_parameters(float jogging_vel, float jogging_accel, float jogging_dist)
{
	jog_vel.set(jogging_vel);
	jog_accel.set(jogging_accel);
	jog_dist.set(jogging_dist);
}

void CableRobot::set_velocity_limit(float velocity_max)
{
	limit_velocity.set(velocity_max);
}

void CableRobot::set_accel_limit(float accel_max)
{
	limit_acceleration.set(accel_max);
}

/**
 * @brief Set minimum and maximum travel bounds .
 *
 * @param (float)  min: minimum bounds (in mm)
 * @param (float)  max: maximum bounds (in mm)
 */
void CableRobot::set_bounds(float min, float max)
{
	bounds_min.set(min);
	bounds_max.set(max);
}

bool CableRobot::is_torque_in_limits()
{
	auto torque_measured = motor->get()->Motion.TrqMeasured.Value();
	//info_torque_actual.set(ofToString(torque_measured));
	if (torque_measured > limit_torque_max.get() || torque_measured < limit_torque_min.get()) {
		ofLogWarning(__FUNCTION__) << "\tRobot " << ofToString(motor->get_motor_id()) << " is OUT OF TORQUE RANGE with value of " << ofToString(torque_measured) << endl;
		return false;
	}
	return true;
}
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

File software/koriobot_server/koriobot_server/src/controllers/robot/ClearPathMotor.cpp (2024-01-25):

#include "ClearPathMotor.h"

ClearPathMotor::ClearPathMotor(SysManager& SysMgr, INode* node):
	m_node(node),
	m_sysMgr(SysMgr) {

	printf("   Node[%d]: type=%d\n", m_node->Info.Ex.Addr(), m_node->Info.NodeType());
	printf("            userID: %s\n", m_node->Info.UserID.Value());
	printf("        FW version: %s\n", m_node->Info.FirmwareVersion.Value());
	printf("          Serial #: %d\n", m_node->Info.SerialNumber.Value());
	printf("             Model: %s\n", m_node->Info.Model.Value());
	printf("        Resolution: %d\n", m_node->Info.PositioningResolution.Value());
	printf("      Is E-Stopped: %s\n", is_estopped() ? "TRUE" : "FALSE");
	printf("        Is Enabled: %s\n", is_enabled() ? "TRUE" : "FALSE");
	printf("          Is Homed: %s\n", m_node->Motion.Homing.WasHomed() ? "TRUE":"FALSE");
	printf("  Current Position: %d\n\n", get_position());

	set_motion_params();
}

ClearPathMotor::~ClearPathMotor() {
	// Disable the node and wait for it to disable
	m_node->EnableReq(false);

	// Poll the status register to confirm the node's disable
	time_t timeout;
	timeout = time(NULL) + 3;
	m_node->Status.RT.Refresh();
	while (m_node->Status.RT.Value().cpm.Enabled) {
		if (time(NULL) > timeout) {
			printf("Error: Timed out waiting for disable\n");
			return;
		}
		m_node->Status.RT.Refresh();
	};
}

int ClearPathMotor::get_resolution()
{
	return m_node->Info.PositioningResolution.Value();;
}

void ClearPathMotor::set_motion_params(float imit_velocity, float imit_acceleration, int limit_trq_percent)
{
	// Set the user units to RPM and RPM/s
	m_node->VelUnit(INode::RPM);
	m_node->AccUnit(INode::RPM_PER_SEC);
	m_node->TrqUnit(INode::PCT_MAX);
	
	uint32_t jerk_limit = 3;

	m_node->Motion.VelLimit.Value(imit_velocity);
	m_node->Motion.AccLimit.Value(imit_acceleration);
	m_node->Motion.JrkLimit.Value(jerk_limit);
	m_node->Limits.PosnTrackingLimit.Value(m_node->Info.PositioningResolution.Value() / 4);
	m_node->Limits.TrqGlobal.Value(limit_trq_percent);

	m_node->Motion.TrqMeasured.AutoRefresh(true);
	m_node->Motion.VelMeasured.AutoRefresh(true);
	m_node->Motion.PosnMeasured.AutoRefresh(true);
}

void ClearPathMotor::enable()
{
	if (m_node != NULL) {
		// Clear alerts and node stops
		m_node->Status.AlertsClear();
		m_node->Motion.NodeStop(STOP_TYPE_ABRUPT);
		m_node->Motion.NodeStop(STOP_TYPE_CLR_ALL);

		// Enable the node
		m_node->EnableReq(true);

		// If the node is not currently ready, wait for it to get there
		time_t timeout;
		timeout = time(NULL) + 3;
		// Basic mode - Poll until disabled
		while (!m_node->Status.IsReady()) {
			if (time(NULL) > timeout) {
				ofLogWarning("ClearPathMotor::Enable()") << "Error: Timed out waiting for enable";
				return;
			}
		}
	}
}

void ClearPathMotor::disable()
{
	// Disable the node and wait for it to disable
	m_node->EnableReq(false);

	// Poll the status register to confirm the node's disable
	time_t timeout;
	timeout = time(NULL) + 3;
	m_node->Status.RT.Refresh();
	while (m_node->Status.RT.Value().cpm.Enabled) {
		if (time(NULL) > timeout) {
			printf("Error: Timed out waiting for disable\n");
			return;
		}
		m_node->Status.RT.Refresh();
	};
}

void ClearPathMotor::stop(nodeStopCodes stop_type)
{
	ofLogNotice("ClearPathMotor::stop") << "Stopping ClearPathMotor " << ofToString(m_node->Info.Ex.Addr()) << ".";
	m_node->Motion.NodeStop(stop_type);		// this should clear buffer and stop, but not working with velocity move
	m_node->Motion.NodeStop(stop_type);
	m_node->Motion.MoveVelStart(0);			// ensure stop by setting velocity to zero
	m_node->Motion.MoveVelStart(0);
	m_node->Status.RT.Refresh();
}

void ClearPathMotor::set_e_stop(bool val)
{
	if (val) {
		ofLogNotice("ClearPathMotor::set_e_stop") << "Triggering E-Stop for ClearPathMotor " << ofToString(m_node->Info.Ex.Addr()) << ".";
		m_node->Motion.NodeStop(STOP_TYPE_ESTOP_ABRUPT);
	}
	// Clear the E-Stop
	else {
		// Update the registers
		m_node->Status.RT.Refresh();
		m_node->Status.Alerts.Refresh();
		if (m_node->Status.Alerts.Value().cpm.Common.EStopped) {
			ofLogNotice("ClearPathMotor::clearMotionStop") << "Clearing E-Stop for ClearPathMotor " << ofToString(m_node->Info.Ex.Addr()) << ".";
			m_node->Motion.NodeStopClear();
		}
		else {
			ofLogNotice("ClearPathMotor::clearMotionStop") << "ClearPathMotor " << ofToString(m_node->Info.Ex.Addr()) << " is not E-Stopped.";
		}
	}
}

void ClearPathMotor::set_enabled(bool val)
{
	if (val && !is_enabled()) {
		ofLogNotice("ClearPathMotor::set_enabled") << "Enabling ClearPathMotor " << ofToString(m_node->Info.Ex.Addr()) << ".";
		enable();
	}
	else if (!val) {
		ofLogNotice("ClearPathMotor::set_enabled") << "Disabling ClearPathMotor " << ofToString(m_node->Info.Ex.Addr()) << ".";
		disable();
	}
}

/**
 * @brief Returns either the target or actual motor position (in counts).
 * 
 * @param (bool)  get_actual_pos: returns the current actual position if true, the target position if false. True by default.
 * 
 * @return (int) motor position (in counts) 
 */
int ClearPathMotor::get_position(bool get_actual_pos)
{
	if (get_actual_pos) {
		m_node->Motion.PosnMeasured.Refresh();
		return int64_t(m_node->Motion.PosnMeasured.Value());
	}
	else {
		m_node->Motion.PosnCommanded.Refresh();
		return int64_t(m_node->Motion.PosnCommanded.Value());
	}
}

/**
 * @brief Get the desired velocity.
 * 
 * @return (float) desired velocity (RPM) 
 */
float ClearPathMotor::get_velocity()
{
	return m_node->Motion.VelLimit.Value();
}

/**
 * @brief Get the actual, measured velocity.
 * 
 * @return (float)  actual velocity (RPM)
 */
float ClearPathMotor::get_velocity_actual()
{
	return m_node->Motion.VelMeasured.Value();
}

/**
 * @brief Set the desired velocity.
 * 
 * @param (float)  val: desired velocity (RPM)
 */
void ClearPathMotor::set_velocity(float val)
{
	m_node->Motion.VelLimit.Value(val);
}

/**
 * @brief Get the desired acceleration.
 *
 * @return (float)  desired acceleration (RPM/s)
 */
float ClearPathMotor::get_acceleration()
{
	return m_node->Motion.AccLimit.Value();
}

/**
 * @brief Set the desired acceleration.
 * 
 * @param (float)  val: desired acceleration (RPM/s)
 */
void ClearPathMotor::set_acceleration(float val)
{
	m_node->Motion.AccLimit.Value(val);
}

/**
 * @brief Issues a trapezoidal position move. Will come to complete stop when target is reached.
 *
 * @param (int)  target_pos: target motor position in motor counts.
 * @param (bool)  is_absolute: target is abosulte or relative to current postion.
 * @param (bool)  add_dwell: whether to delay the next move being issued by DwellMs after this move profile completes.
 */
void ClearPathMotor::move_position(int target_pos, bool is_absolute, bool add_dwell)
{
	m_node->Motion.MovePosnStart(target_pos, is_absolute, add_dwell);
}
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
